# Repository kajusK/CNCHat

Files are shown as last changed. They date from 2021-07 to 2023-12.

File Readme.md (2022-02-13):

# LinuxCNC Shield for OrangePi

This repo contains a HW design files for OrangePi CNC shield for making the
OrangePi a LinuxCNC machine.

The [allwincnc](https://allwincnc.github.io/) project can be used to do the
realtime heavy lifting (stepper control) while the OrangePi does the slower
tasks (kinematics calculations,...).

More details about making this all work with a real CNC machine can be found
on [my blog](https://deadbadger.cz/projects/linuxcnc-on-orangepi)

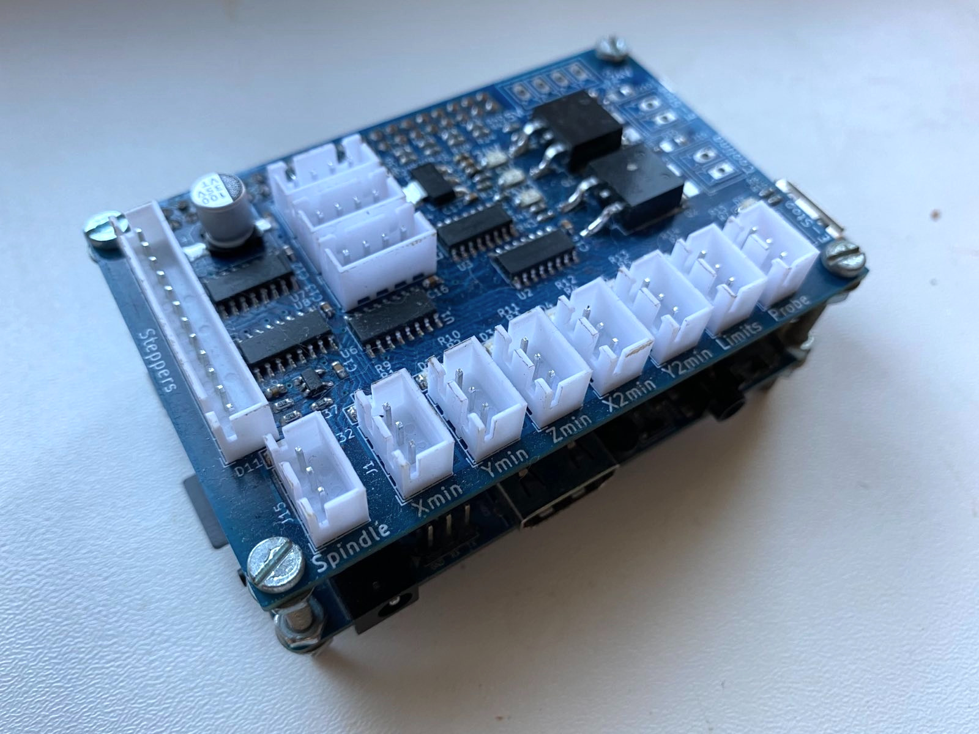
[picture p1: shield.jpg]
shield


## Features
* 5 stepper controllers (direction and step signals) supported
* 3 encoders inputs
* Spindle control - both PWM and 0-10 V outputs
* 6 limit switches (endstops, home position,...)
* Probe sensor input
* Stop button input
* 2 power outputs (cooling, ESTOP,...), up to 24 V
* Incidator leds on inputs and outputs for easier debugging
* Up to 15 V inputs protection
* Selectable 3.3/5 V power for limit switches
* OrangePi can be powered directly from the board (dedicated 5 V input) and vice versa.

## Connectors
### J21 Steppers
| Pin | Signal |
|-----|---|
| 1 | GND |
| 2 | ~Enable |
| 3 | Y2 dir |
| 4 | Y2 step |
| 5 | X2 dir |
| 6 | X2 step |
| 7 | Z dir |
| 8 | Z step |
| 9 | Y dir |
| 10 | Y step |
| 11 | X dir |
| 12 | X step |

### J15 spindle
| Pin | Signal |
|-----|---|
| 1 | GND |
| 2 | 0-10 V |
| 3 | PWM |

### J11, J12, J13 Encoders
| Pin | Signal |
|-----|---|
| 1 | GND |
| 2 | B |
| 3 | A |
| 4 | 5 V |

### J1-J7 Inputs
| Pin | Signal |
|-----|---|
| 1 | 5/3.3 V |
| 2 | GND |
| 3 | signal (with pull-up) |

## OrangePi Pinout

### Steppers
| | X | Y | Z | X2 | Y2 |
| :--  | :--: | :--: | :--: | :--: | :--: |
| Step | PA0  | PA12 | PA13 | PC4  | PA14 |
| Dir  | PA6  | PA1  | PA11 | PD14 | PC7  |

### Encoders
| | X | Y | Z |
| :--  | :--: | :--: | :--: |
| A | PA8  | PA18 | PC2  |
| B | PA9  | PG9  | PA21 |

### Limit switches
| Xmin | Ymin | Zmin | X2min| Y2min| Limits |
| :--: | :--: | :--: | :--: | :--: | :--: |
| PA2  | PC1  | PA19 | PA7  | PG8  | PC3 |

### Others
| Enable | Spindle | Cooling | Probe | ESTOP in | ESTOP out |
| :--: | :--: | :--: | :--: | :--: | :--: |
| PA3  | PC0  | PG7 | PA10  | PA20  | PG6 |

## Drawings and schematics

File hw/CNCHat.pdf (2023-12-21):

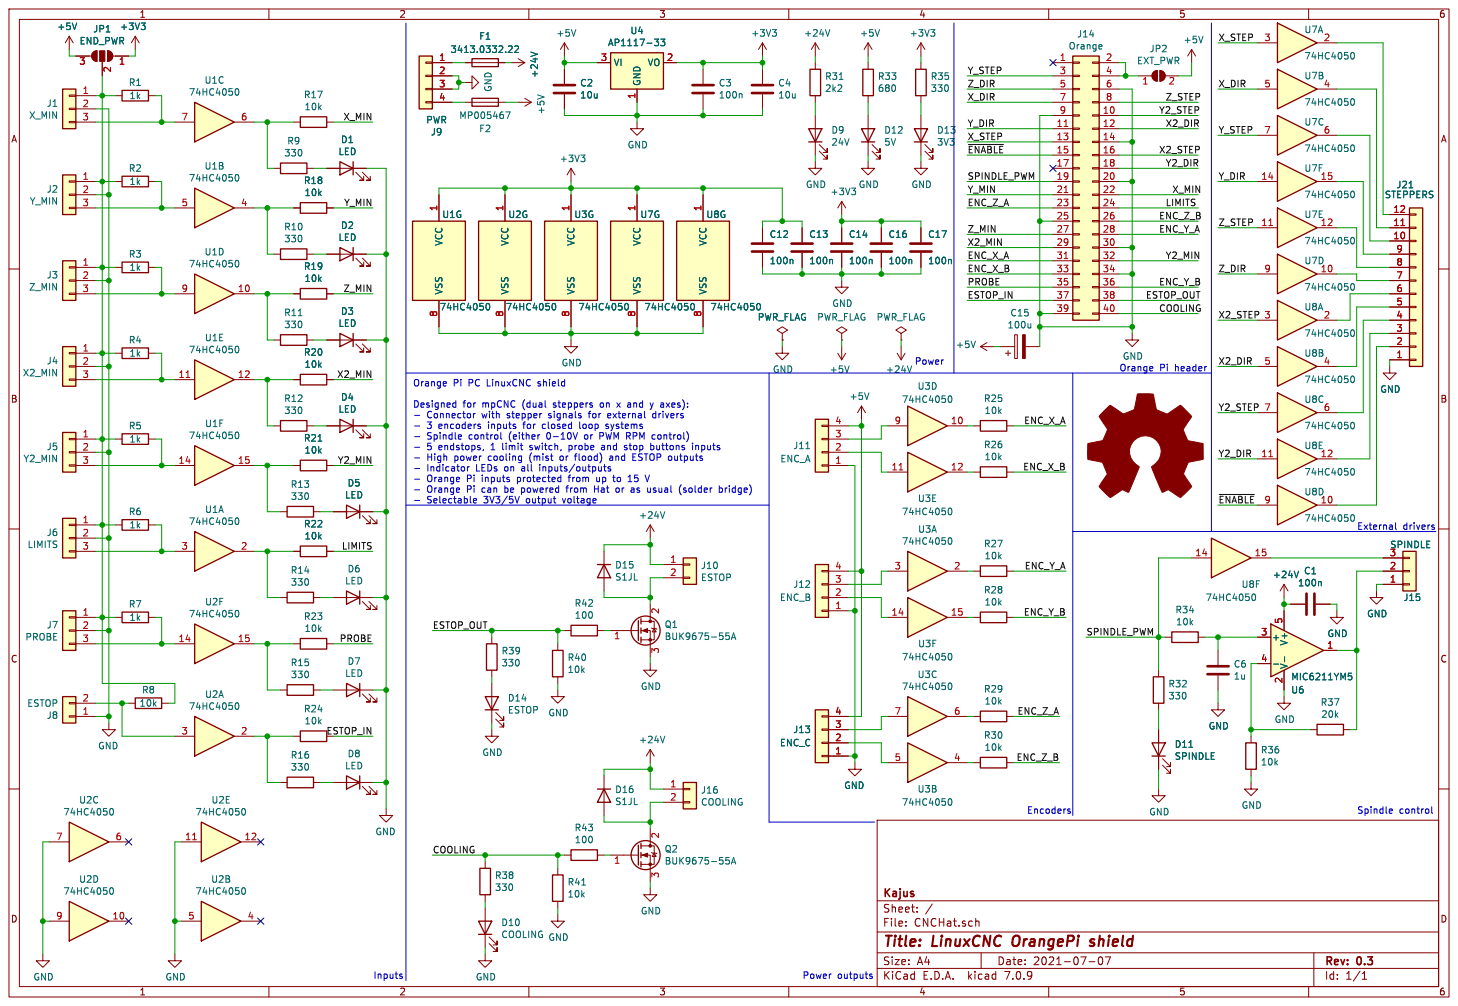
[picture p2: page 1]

- 3 encoders inputs for closed loop systems
- Orange Pi can be powered from Hat or as usual (solder bridge)

Id: 1/1 Title: LinuxCNC OrangePi shield

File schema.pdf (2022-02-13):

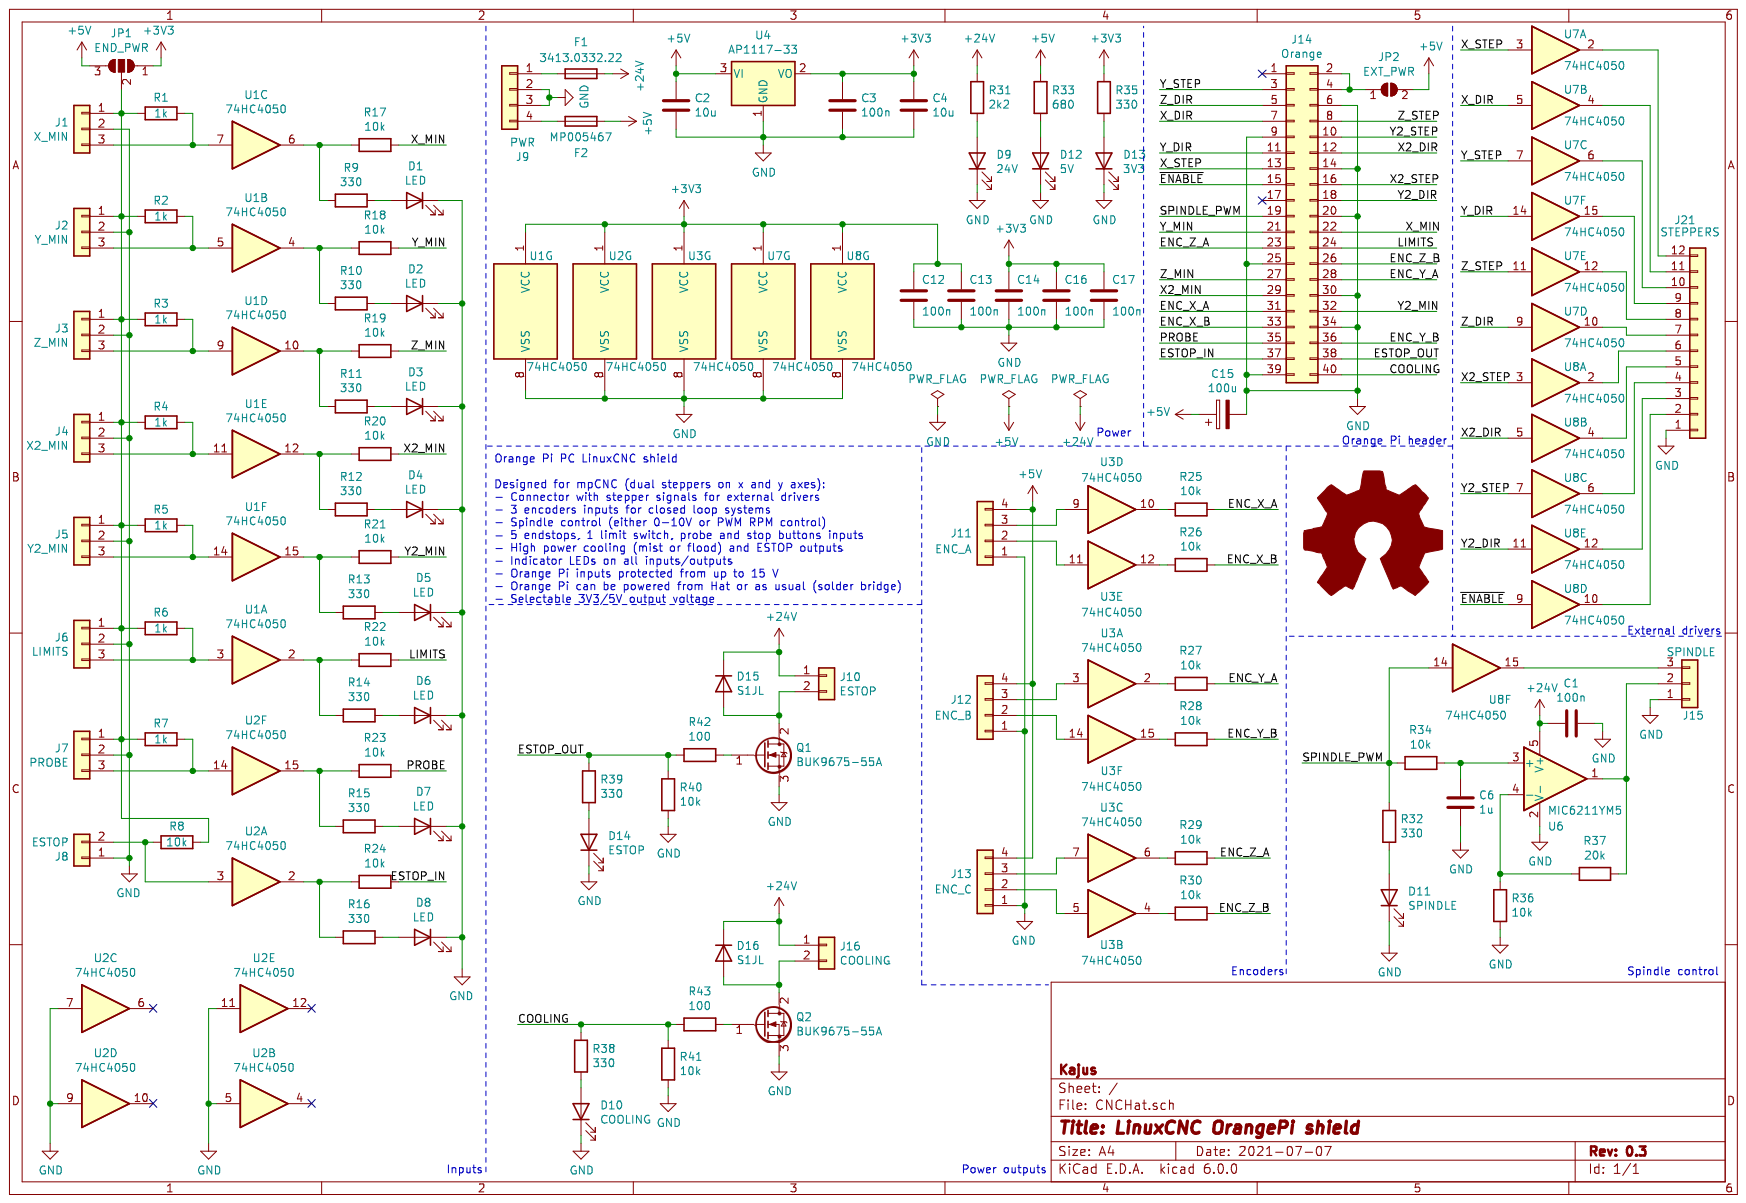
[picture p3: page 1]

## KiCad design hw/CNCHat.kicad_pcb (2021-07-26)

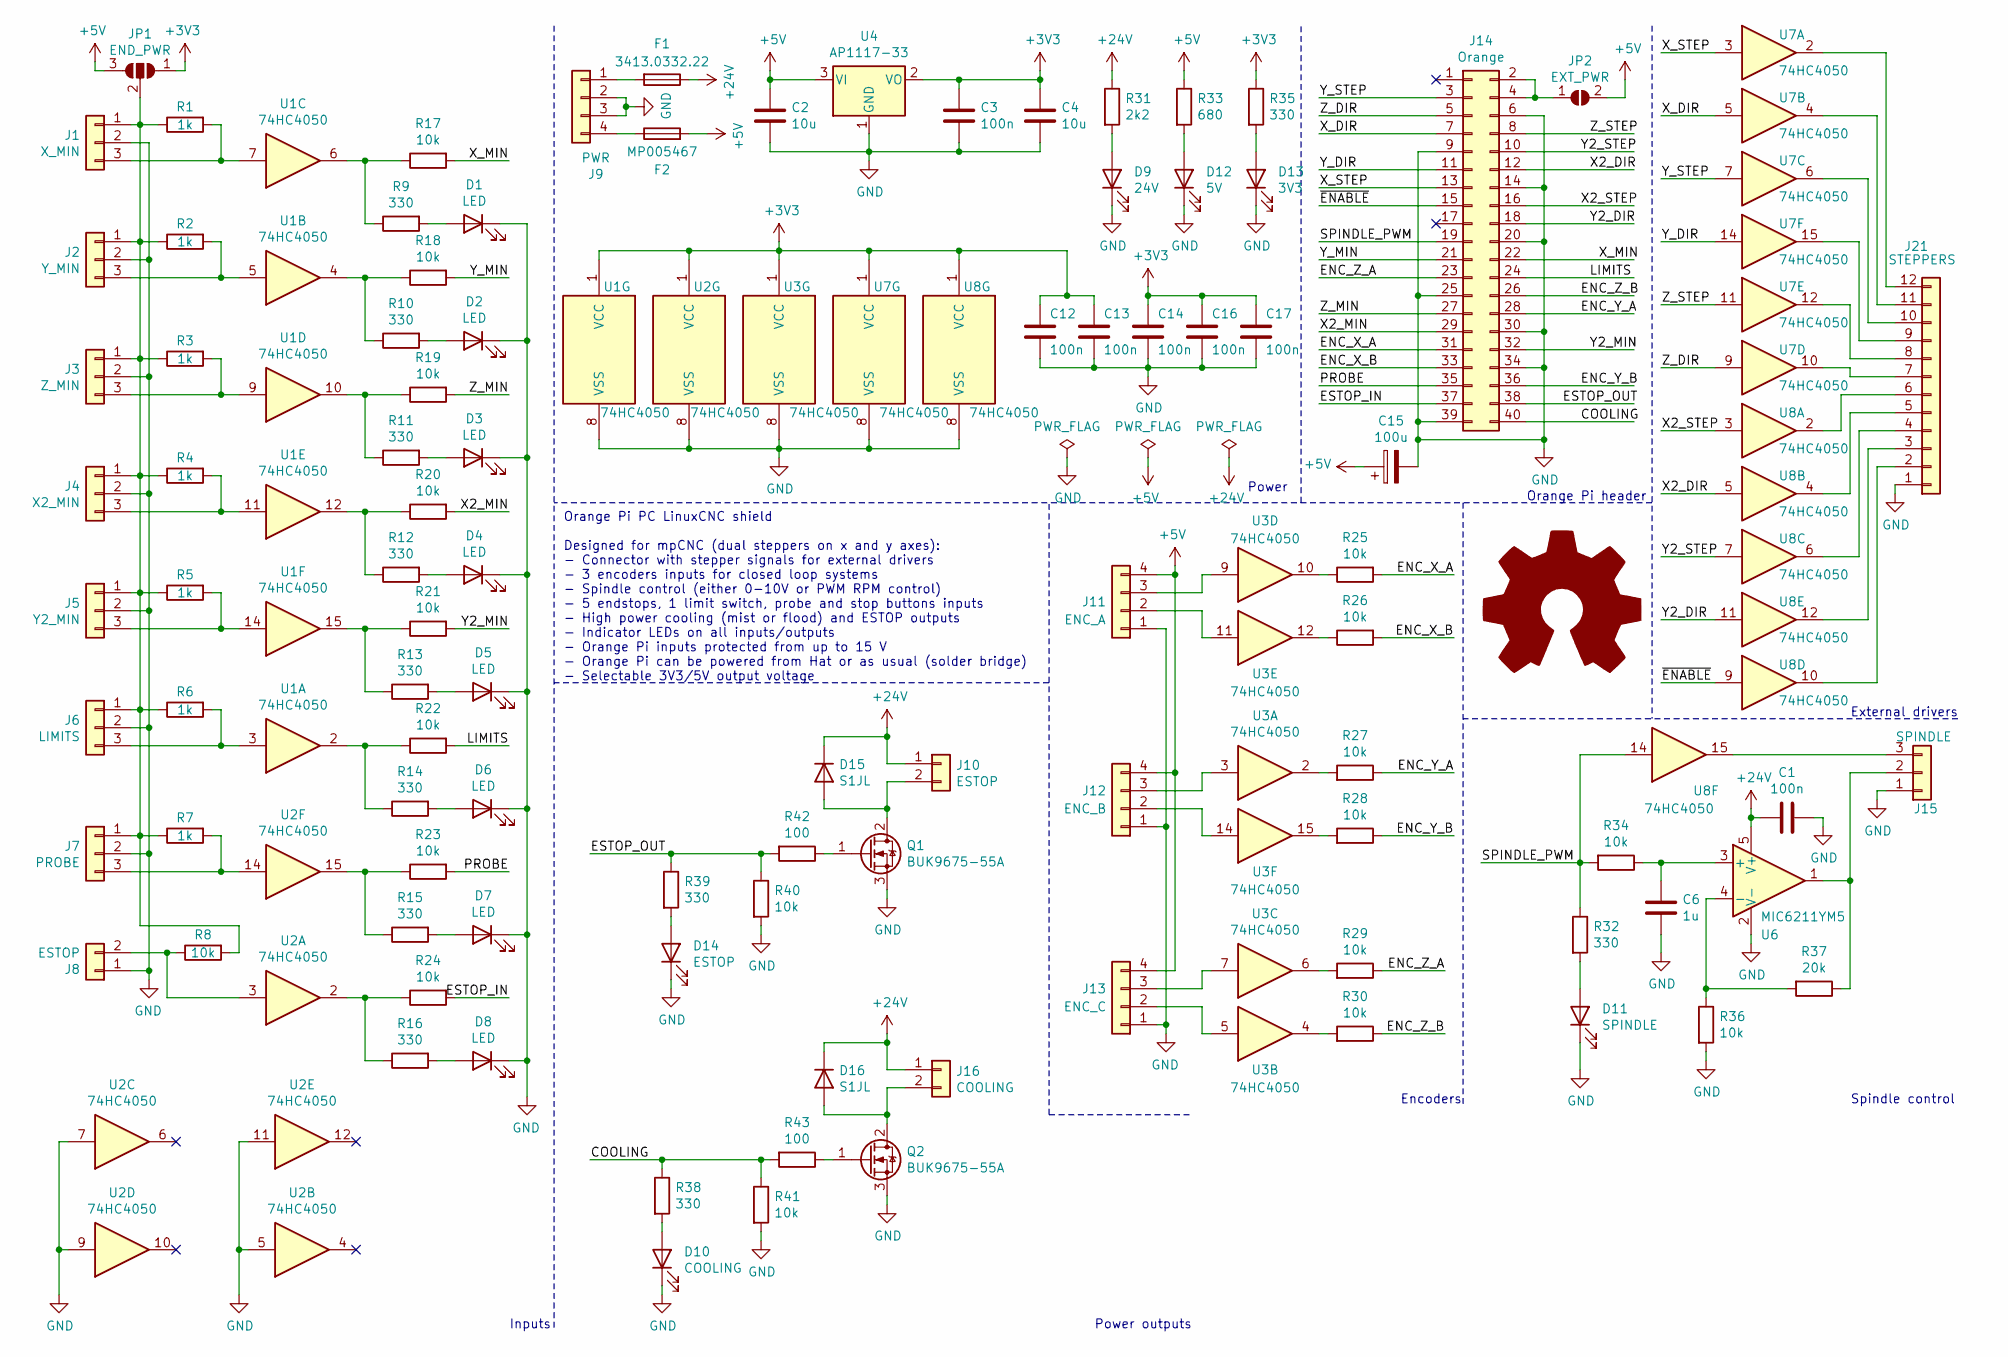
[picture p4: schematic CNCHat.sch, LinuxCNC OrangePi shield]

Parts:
C1, C3, C12, C13, C14, C16, C17: 100n; C_0603_1608Metric
C2, C4: 10u; C_0603_1608Metric
C6: 1u; C_0603_1608Metric
C15: 100u; CP_Elec_8x10.5
D1, D2, D3, D4, D5, D6, D7, D8: LED; LED_1206_3216Metric
D9: 24V; LED_1206_3216Metric
D10: COOLING; LED_1206_3216Metric
D11: SPINDLE; LED_1206_3216Metric
D12: 5V; LED_1206_3216Metric
D13: 3V3; LED_1206_3216Metric
D14: ESTOP; LED_1206_3216Metric
D15, D16: S1JL; D_SMA
F1: 3413.0332.22; Fuse_1206_3216Metric
F2: MP005467; Fuse_1206_3216Metric
J1: X_MIN; JST_XH_B3B-XH-A_1x03_P2.50mm_Vertical
J2: Y_MIN; JST_XH_B3B-XH-A_1x03_P2.50mm_Vertical
J3: Z_MIN; JST_XH_B3B-XH-A_1x03_P2.50mm_Vertical
J4: X2_MIN; JST_XH_B3B-XH-A_1x03_P2.50mm_Vertical
J5: Y2_MIN; JST_XH_B3B-XH-A_1x03_P2.50mm_Vertical
J6: LIMITS; JST_XH_B3B-XH-A_1x03_P2.50mm_Vertical
J7: PROBE; JST_XH_B3B-XH-A_1x03_P2.50mm_Vertical
J8: ESTOP; JST_XH_B2B-XH-A_1x02_P2.50mm_Vertical
J9: PWR; PhoenixContact_MCV_1,5_4-G-3.5_1x04_P3.50mm_Vertical
J10: ESTOP; PhoenixContact_MCV_1,5_2-G-3.5_1x02_P3.50mm_Vertical
J11: ENC_A; JST_XH_B4B-XH-A_1x04_P2.50mm_Vertical
J12: ENC_B; JST_XH_B4B-XH-A_1x04_P2.50mm_Vertical
J13: ENC_C; JST_XH_B4B-XH-A_1x04_P2.50mm_Vertical
J14: Orange; PinSocket_2x20_P2.54mm_Vertical
J15: SPINDLE; JST_XH_B3B-XH-A_1x03_P2.50mm_Vertical
J16: COOLING; PhoenixContact_MCV_1,5_2-G-3.5_1x02_P3.50mm_Vertical
J21: STEPPERS; JST_XH_B12B-XH-A_1x12_P2.50mm_Vertical
JP1: END_PWR; SolderJumper-3_P2.0mm_Open_TrianglePad1.0x1.5mm_NumberLabels
JP2: EXT_PWR; SolderJumper-2_P1.3mm_Open_TrianglePad1.0x1.5mm
Q1, Q2: BUK9675-55A; TO-263-2
R1, R2, R3, R4, R5, R6, R7: 1k; R_0603_1608Metric
R8, R17, R18, R19, R20, R21, R22, R23, R24, R25, R26, R27, R28, R29, R30, R34, R36, R40, R41: 10k; R_0603_1608Metric
R9, R10, R11, R12, R13, R14, R15, R16, R32, R35, R38, R39: 330; R_0603_1608Metric
R31: 2k2; R_0603_1608Metric
R33: 680; R_0603_1608Metric
R37: 20k; R_0603_1608Metric
R42, R43: 100; R_0603_1608Metric
U1, U2, U3, U7, U8: 74HC4050; SOIC-16_3.9x9.9mm_P1.27mm
U4: AP1117-33; SOT-223-3_TabPin2
U6: MIC6211YM5; SOT-23-5

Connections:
+3V3: C3.1, C4.1, C12.1, C13.1, C14.1, C16.1, C17.1, JP1.1 (A), R35.1, U1.1 (VCC), U2.1 (VCC), U3.1 (VCC), U4.2 (VO), U7.1 (VCC), U8.1 (VCC)
+5V: C2.1, C15.1, F2.2, J11.4, J12.4, J13.4, JP1.3 (B), JP2.2 (B), R33.1, U4.3 (VI)
+24V: C1.2, D15.1 (K), D16.1 (K), F1.1, J10.1, J16.1, R31.1, U6.5 (V+)
/COOLING: J14.40, R38.1, R41.1, R43.2
/ENC_X_A: J14.31, R25.2
/ENC_X_B: J14.33, R26.2
/ENC_Y_A: J14.28, R27.1
/ENC_Y_B: J14.36, R28.1
/ENC_Z_A: J14.23, R29.1
/ENC_Z_B: J14.26, R30.1
/ESTOP_IN: J14.37, R24.2
/ESTOP_OUT: J14.38, R39.1, R40.1, R42.2
/LIMITS: J14.24, R22.2
/PROBE: J14.35, R23.2
/SPINDLE_PWM: J14.19, R32.1, R34.2, U8.14
/X2_DIR: J14.12, U8.5
/X2_MIN: J14.29, R20.2
/X2_STEP: J14.16, U8.3
/X_DIR: J14.7, U7.5
/X_MIN: J14.22, R17.2
/X_STEP: J14.13, U7.3
/Y2_DIR: J14.18, U8.11
/Y2_MIN: J14.32, R21.2
/Y2_STEP: J14.10, U8.7
/Y_DIR: J14.11, U7.14
/Y_MIN: J14.21, R18.2
/Y_STEP: J14.3, U7.7
/Z_DIR: J14.5, U7.9
/Z_MIN: J14.27, R19.2
/Z_STEP: J14.8, U7.11
/~ENABLE: J14.15, U8.9
GND: C1.1, C2.2, C3.2, C4.2, C6.2, C12.2, C13.2, C14.2, C15.2, C16.2, C17.2, D1.1 (K), D2.1 (K), D3.1 (K), D4.1 (K), D5.1 (K), D6.1 (K), D7.1 (K), D8.1 (K), D9.1 (K), D10.1 (K), D11.1 (K), D12.1 (K), D13.1 (K), D14.1 (K), J1.2, J2.2, J3.2, J4.2, J5.2, J6.2, J7.2, J8.1, J9.2, J9.3, J11.1, J12.1, J13.1, J14.6, J14.9, J14.14, J14.20, J14.25, J14.30, J14.34, J14.39, J15.1, J21.1, Q1.3 (S), Q2.3 (S), R36.2, R40.2, R41.2, U1.8 (VSS), U2.5, U2.7, U2.8 (VSS), U2.9, U2.11, U3.8 (VSS), U4.1 (GND), U6.2 (V-), U7.8 (VSS), U8.8 (VSS)
unnamed: C6.1, R34.1, U6.3 (+)
unnamed: D1.2 (A), R9.2
unnamed: D2.2 (A), R10.2
unnamed: D3.2 (A), R11.2
unnamed: D4.2 (A), R12.2
unnamed: D5.2 (A), R13.2
unnamed: D6.2 (A), R14.2
unnamed: D7.2 (A), R15.2
unnamed: D8.2 (A), R16.2
unnamed: D9.2 (A), R31.2
unnamed: D10.2 (A), R38.2
unnamed: D11.2 (A), R32.2
unnamed: D12.2 (A), R33.2
unnamed: D13.2 (A), R35.2
unnamed: D14.2 (A), R39.2
unnamed: D15.2 (A), J10.2, Q1.2 (D)
unnamed: D16.2 (A), J16.2, Q2.2 (D)
unnamed: F1.2, J9.1
unnamed: F2.1, J9.4
unnamed: J1.1, J2.1, J3.1, J4.1, J5.1, J6.1, J7.1, JP1.2 (C), R1.1, R2.1, R3.1, R4.1, R5.1, R6.1, R7.1, R8.2
unnamed: J1.3, R1.2, U1.7
unnamed: J2.3, R2.2, U1.5
unnamed: J3.3, R3.2, U1.9
unnamed: J4.3, R4.2, U1.11
unnamed: J5.3, R5.2, U1.14
unnamed: J6.3, R6.2, U1.3
unnamed: J7.3, R7.2, U2.14
unnamed: J8.2, R8.1, U2.3
unnamed: J11.2, U3.11
unnamed: J11.3, U3.9
unnamed: J12.2, U3.14
unnamed: J12.3, U3.3
unnamed: J13.2, U3.5
unnamed: J13.3, U3.7
unnamed: J14.2, J14.4, JP2.1 (A)
unnamed: J15.2, R37.1, U6.1
unnamed: J15.3, U8.15
unnamed: J21.2, U8.10
unnamed: J21.3, U8.12
unnamed: J21.4, U8.6
unnamed: J21.5, U8.4
unnamed: J21.6, U8.2
unnamed: J21.7, U7.10
unnamed: J21.8, U7.12
unnamed: J21.9, U7.15
unnamed: J21.10, U7.6
unnamed: J21.11, U7.4
unnamed: J21.12, U7.2
unnamed: Q1.1 (G), R42.1
unnamed: Q2.1 (G), R43.1
unnamed: R10.1, R18.1, U1.4
unnamed: R11.1, R19.1, U1.10
unnamed: R12.1, R20.1, U1.12
unnamed: R13.1, R21.1, U1.15
unnamed: R14.1, R22.1, U1.2
unnamed: R15.1, R23.1, U2.15
unnamed: R16.1, R24.1, U2.2
unnamed: R9.1, R17.1, U1.6
unnamed: R25.1, U3.10
unnamed: R26.1, U3.12
unnamed: R27.2, U3.2
unnamed: R28.2, U3.15
unnamed: R29.2, U3.6
unnamed: R30.2, U3.4
unnamed: R36.1, R37.2, U6.4 (-)

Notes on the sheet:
Inputs
Encoders
External drivers
Orange Pi header
Spindle control
Orange Pi PC LinuxCNC shield Designed for mpCNC (dual steppers on x and y axes): - Connector with stepper signals for external drivers - 3 encoders inputs for closed loop systems - Spindle control (either 0-10V or PWM RPM control) - 5 endstops, 1 limit switch, probe and stop buttons inputs - High p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
Power
Power outputs

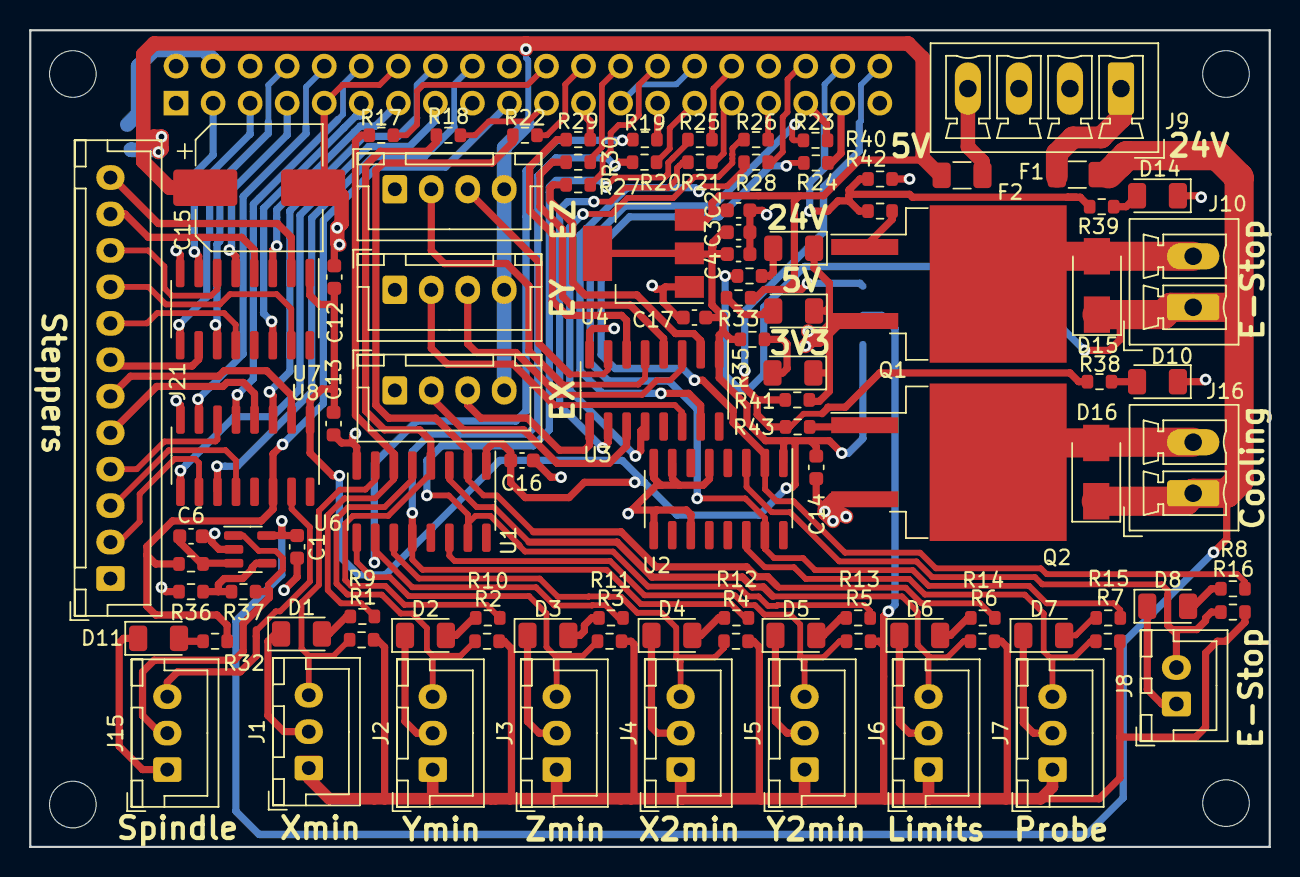
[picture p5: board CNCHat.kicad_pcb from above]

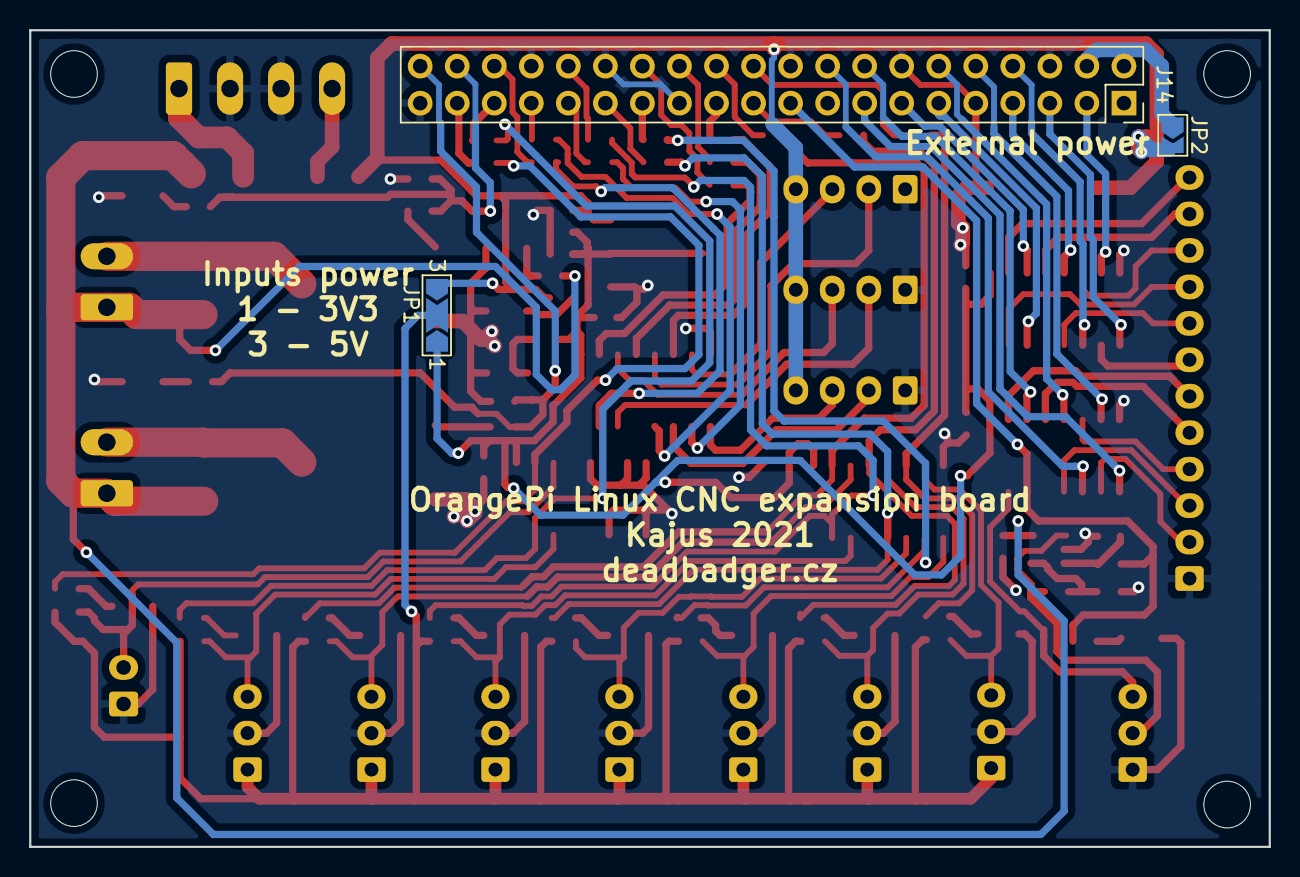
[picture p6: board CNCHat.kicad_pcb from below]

Board: 2 copper layers, 85.0 x 56.0 mm, 100 parts (3 on the bottom side), 97 nets.

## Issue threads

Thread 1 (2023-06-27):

questions

turuwhiska, 2023-06-27:
hi !! the project is very good. allwincnc info says it can run up to 500 kHz. i/o
With this motherboard and the last orange, at what speed would the pulse rate be?
Can it be bought or acquired in any way?

kajusK, 2023-07-03:
Hi @turuwhiska, I've actually haven't tested the full functionality yet due to a lack of time to continue on my CNC project.

The shield should not limit the stepper frequency generated by the Orange in any way, the used buffers are quite fast. I'll try to hook up the driver to the board, give it a proper test over the next weekend and I'll let you know the results.

I have few spare boards I could send you, but with the shipping rates, it's probably cheaper to order new boards from some chinese vendor, all the necessary manufacturing files are in hw/gerbers directory.

turuwhiska, 2023-07-05:
hi @kajusK great I want to try it

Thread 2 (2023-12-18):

3.3/5V outputs

Nosovsergeyal, 2023-12-18:
I can’t figure out where the 3.3/5V outputs are for the stepper motor drivers

kajusK, 2023-12-21:
There's no switch for the steppers output signals, the high level output voltage is fixed to 3.3 V.

 This should work on both the 3.3 and 5 V drivers as the 5V TTL logic specifies a minimum high level input voltage as 2 V, actually the minimum output level for 5 V is 2.7 V, so the 3.3 V output is perfectly within 5 V TTL specs.

I've pushed a PDF schematic to the repo so if you don't have the KiCad installed, you can take a look in schematic anyway to see how it's routed.

There's only one selectable voltage switch - the JP1, it's used to select a power voltage for endstop inputs.

Nosovsergeyal, 2023-12-23:
@kajusK Is there any way I can contact you?

kajusK, 2024-01-01:
I guess you've just contacted me :).

Closed 2023-12-21.

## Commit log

2021-07-26 Initial commit, finished PCB design
    [CNCHat.kicad_pcb, CNCHat.sch]
2022-02-13 Added gerber files for manufacturing
    [CNCHat-B_Cu.gbr, CNCHat-B_Mask.gbr, CNCHat-B_SilkS.gbr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]
2022-02-13 Added readme and schematic
    [CNCHat-B_Cu.gbr, CNCHat-B_Mask.gbr, CNCHat-B_SilkS.gbr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]
2023-12-21 Added schematic in PDF
